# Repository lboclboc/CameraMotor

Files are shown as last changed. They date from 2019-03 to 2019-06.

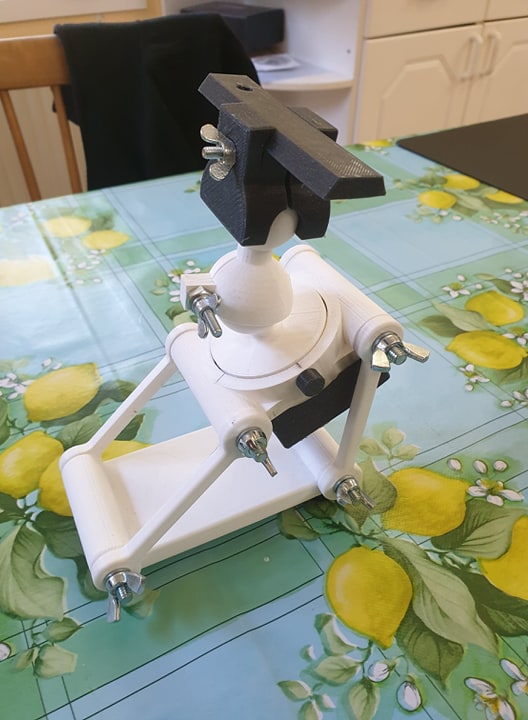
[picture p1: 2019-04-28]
Images/Finished-mount.jpg

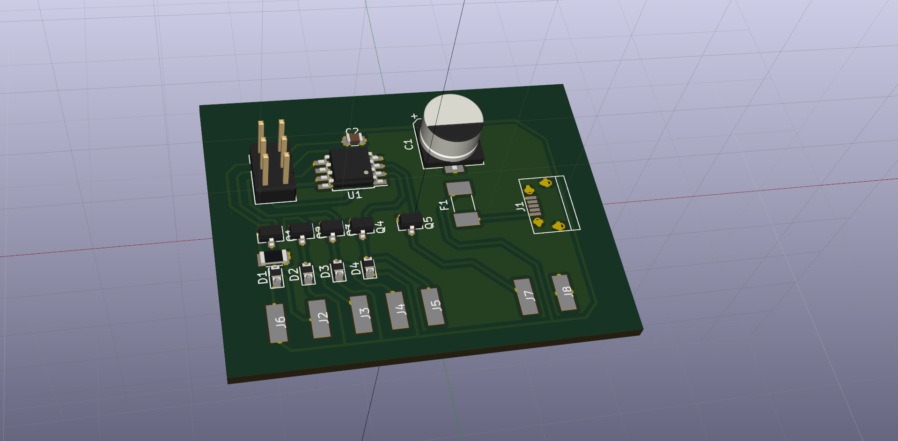
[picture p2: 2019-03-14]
CameraMotor.png

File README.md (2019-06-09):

# CameraMotor
Motorized equatorial camera mount.

This is the code for the EQ-Camera thingiverse mount at https://www.thingiverse.com/thing:3594100.
The current development is focusing on a ESP8266 wifi enabled controller that also will be able to do timelapsing for other purposes 
than astrophotographing.

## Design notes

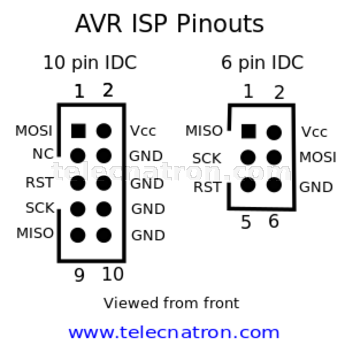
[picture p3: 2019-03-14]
avr-isp-pinout-345x.png

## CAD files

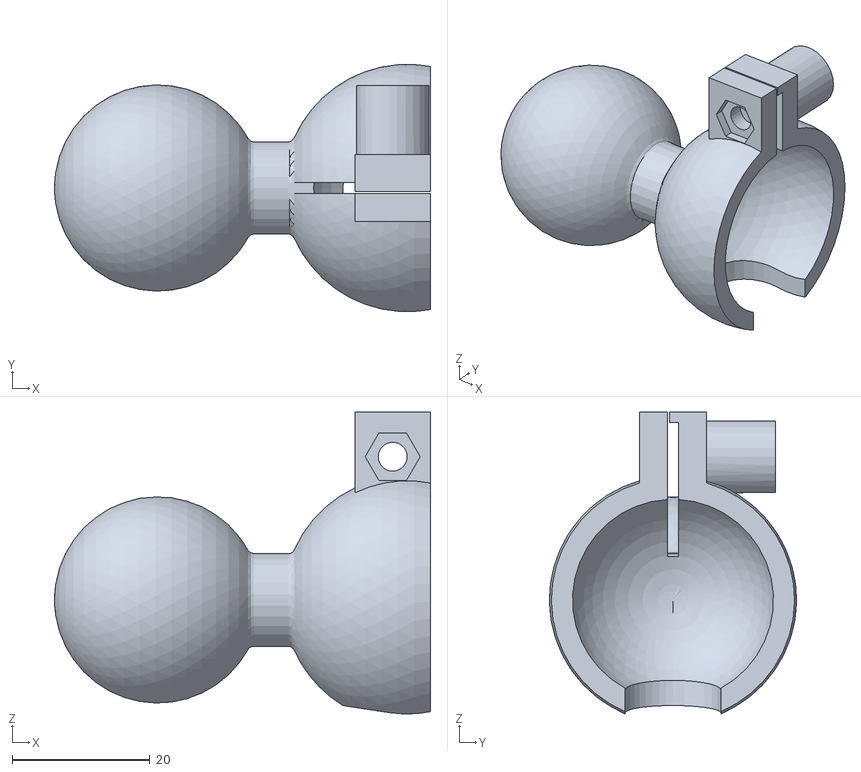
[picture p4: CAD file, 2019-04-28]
3D/CameraMount.stl
54.7 x 35.9 x 43.9

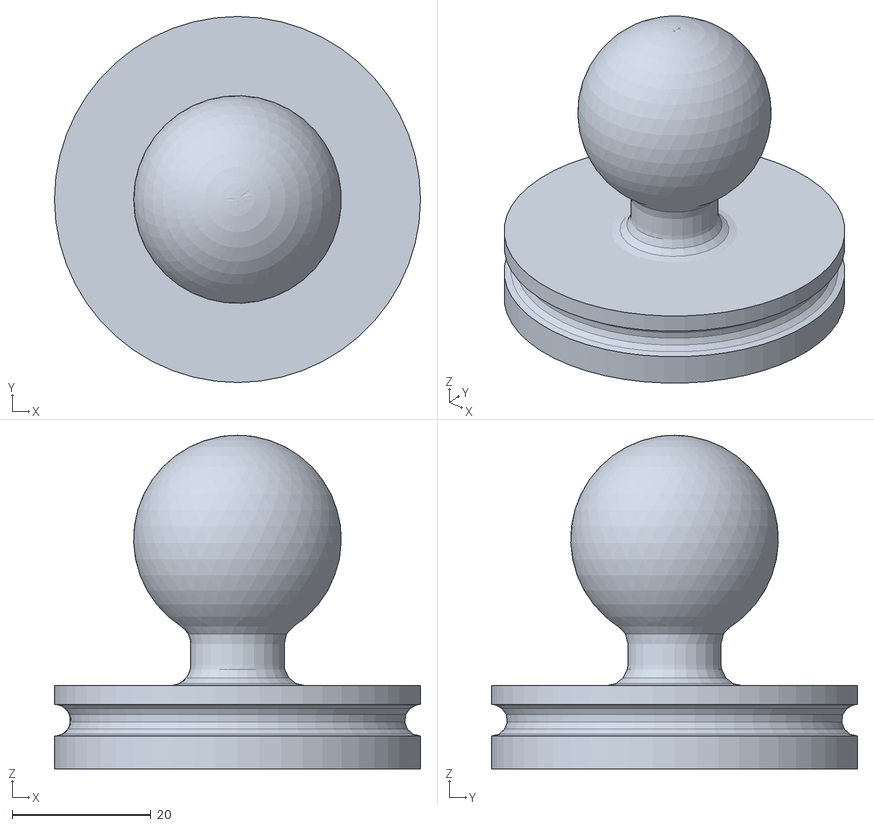
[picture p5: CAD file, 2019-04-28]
3D/turret.stl
52.8 x 52.8 x 48.1

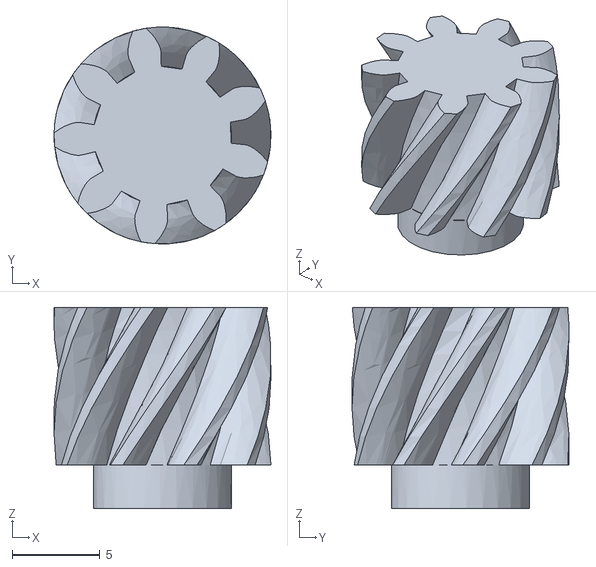
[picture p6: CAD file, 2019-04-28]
3D/Drive.stl
12.4 x 12.4 x 11.5

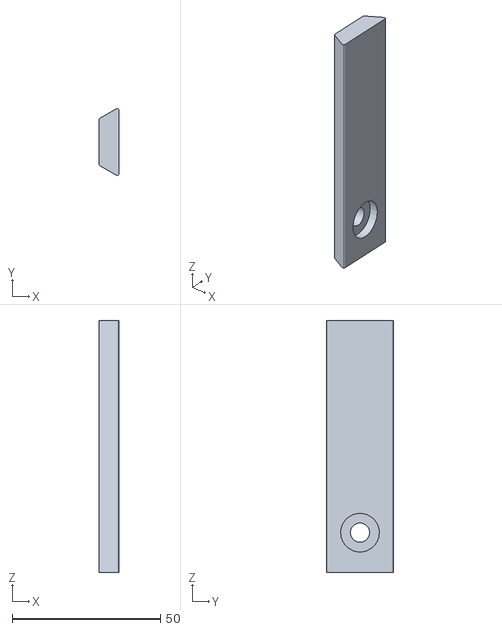
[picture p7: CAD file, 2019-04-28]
3D/CameraRail.stl
6.84 x 22.6 x 85.0

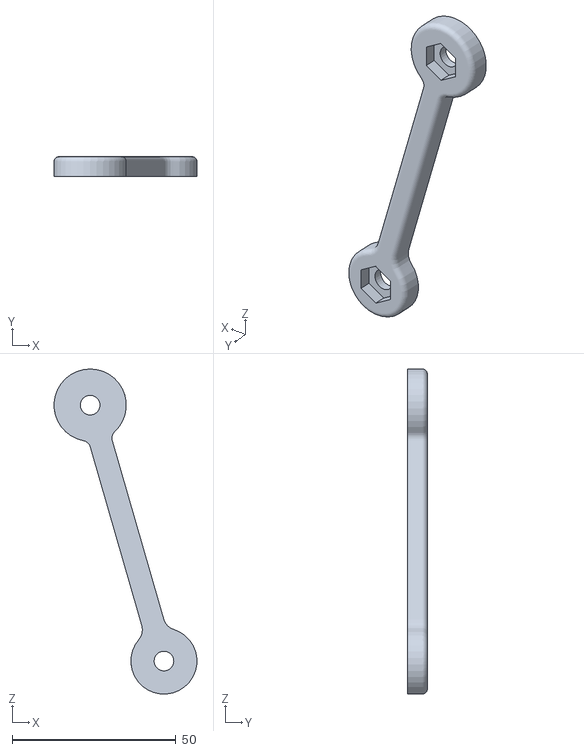
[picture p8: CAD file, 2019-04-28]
3D/arm.stl
43.5 x 6.00 x 99.1

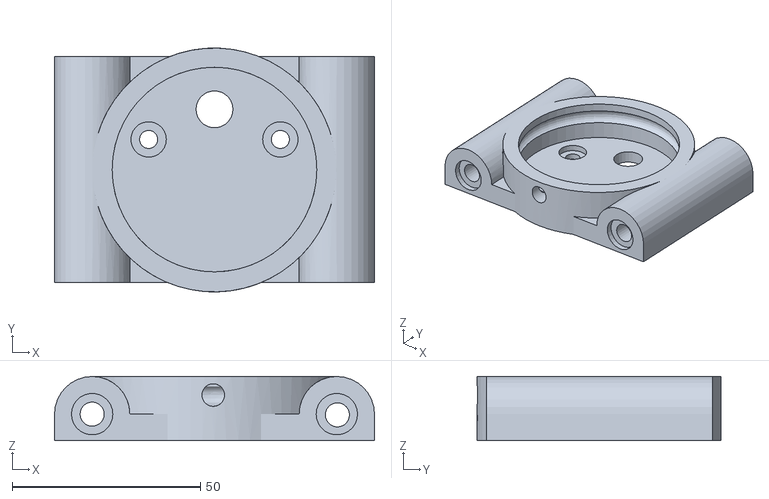
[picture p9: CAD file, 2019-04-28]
3D/topplate.stl
85.0 x 64.8 x 17.0

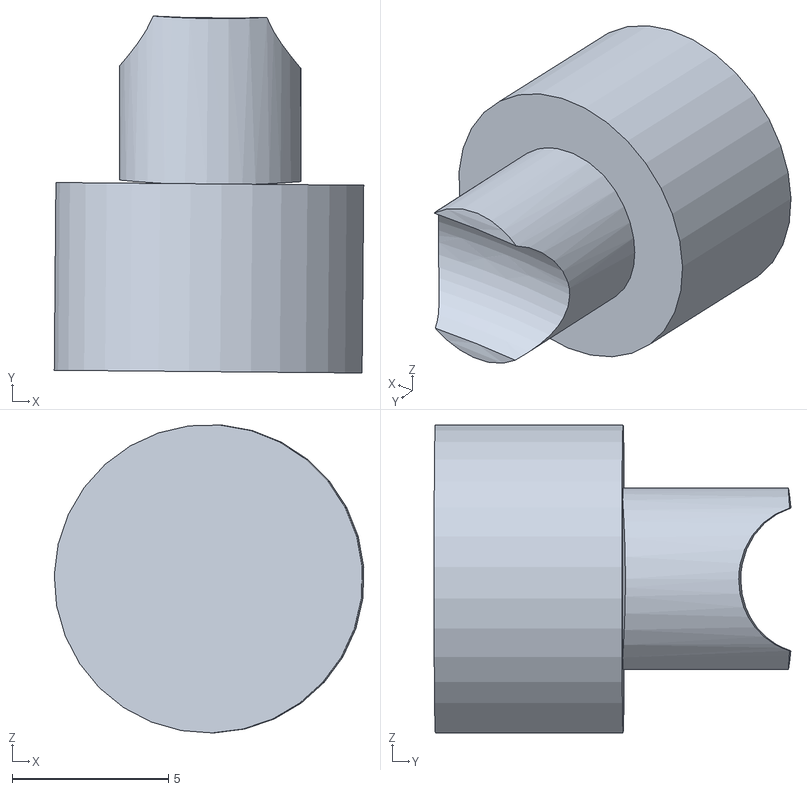
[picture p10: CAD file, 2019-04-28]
3D/Plug.stl
9.89 x 11.4 x 9.84

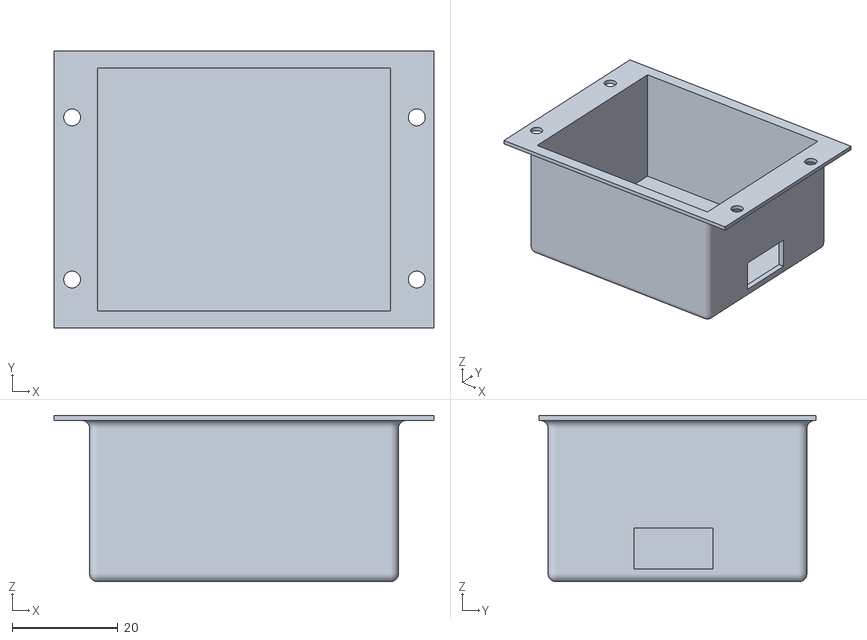
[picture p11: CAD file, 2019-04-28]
3D/PCB-Cover.stl
71.9 x 52.4 x 31.5

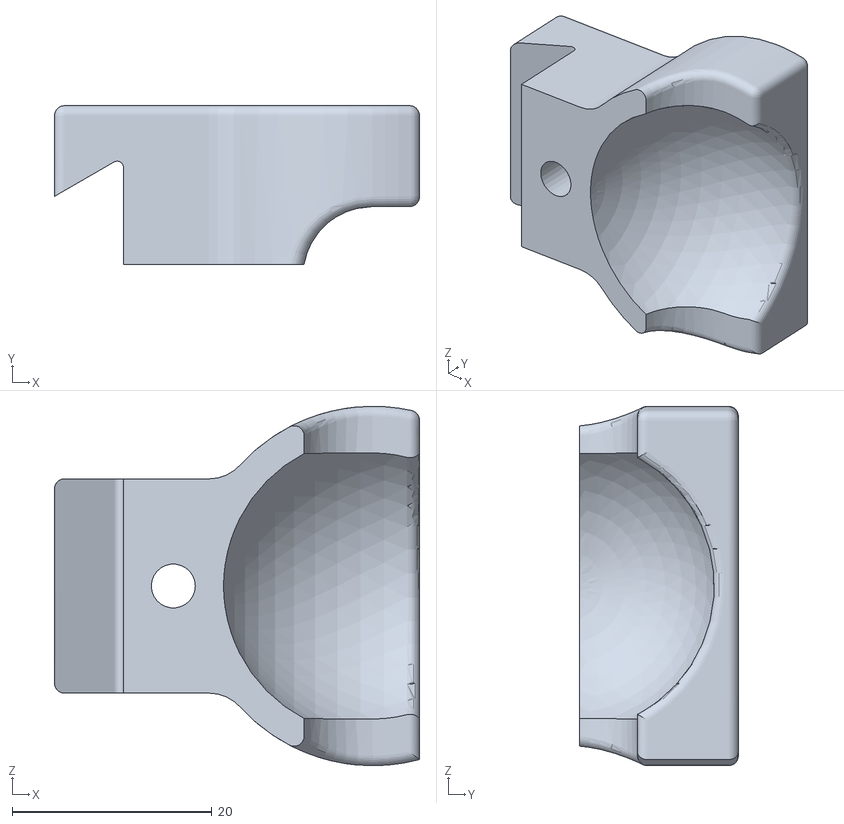
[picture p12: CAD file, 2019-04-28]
3D/CameraTilt.stl
36.6 x 15.9 x 36.0

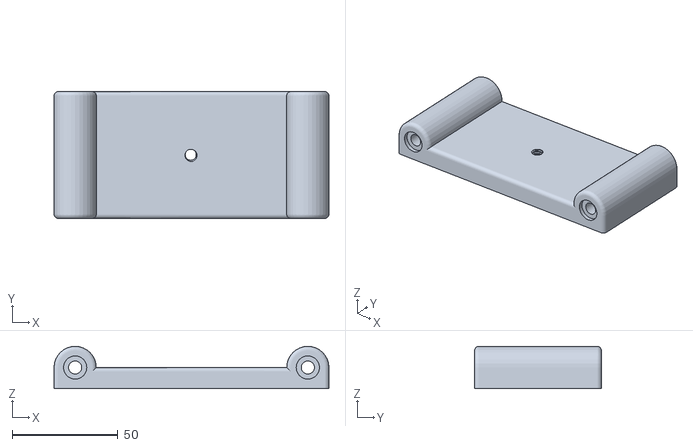
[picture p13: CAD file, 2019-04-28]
3D/bottomplate.stl
130.0 x 60.0 x 20.0

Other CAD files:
3D/CameraMotorMount.FCStd

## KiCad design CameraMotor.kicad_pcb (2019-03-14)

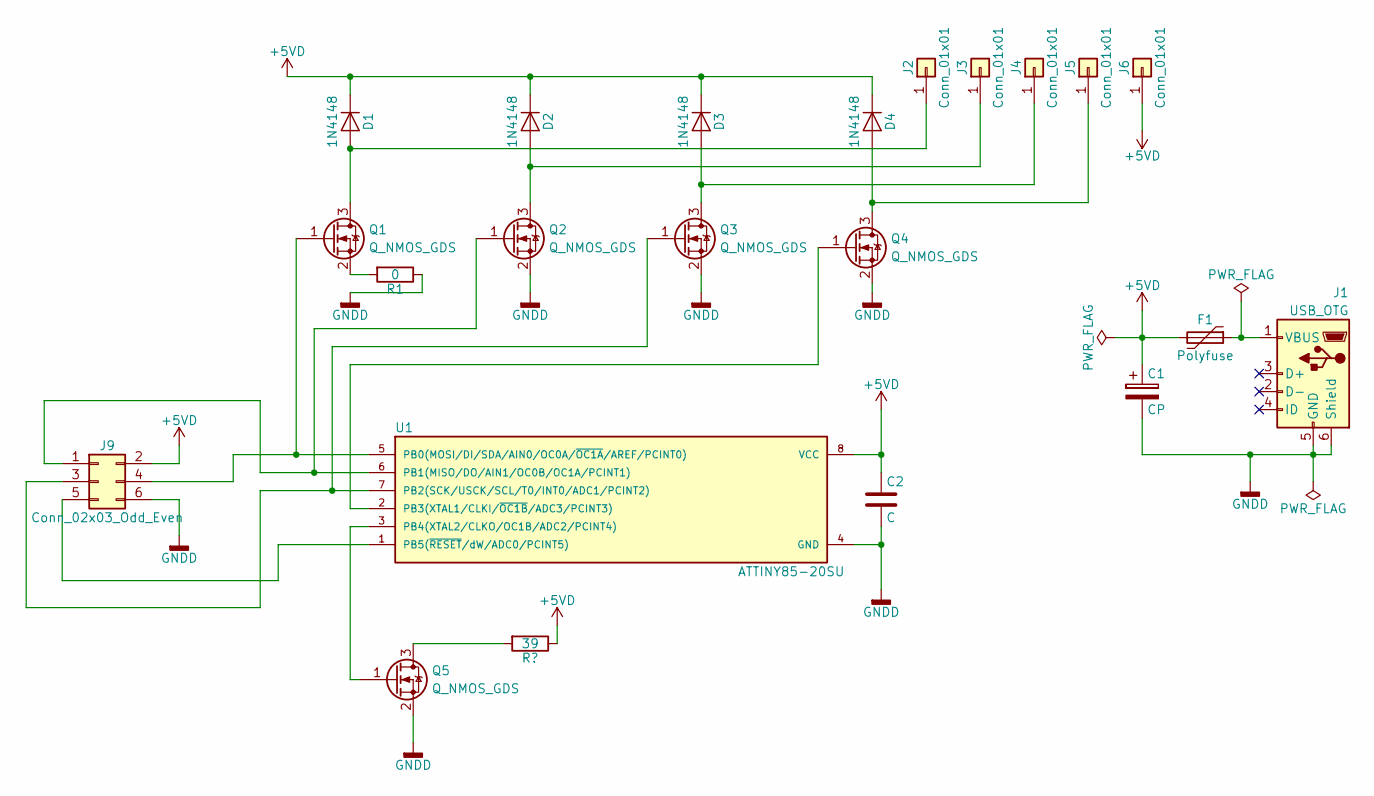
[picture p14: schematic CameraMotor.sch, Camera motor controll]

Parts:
C1: CP; CP_Elec_8x5.4
C2: C; C_0805
D1, D2, D3, D4: 1N4148; D_0805
F1: Polyfuse; Fuse_0679H
J1: USB_OTG; SOIC-28W_7.5x17.9mm_Pitch1.27mm
J2, J3, J4, J5, J6: Conn_01x01; Wire_Pad_5x2mm
J9: Conn_02x03_Odd_Even; Pin_Header_Straight_2x03_Pitch2.54mm
Q1, Q2, Q3, Q4, Q5: Q_NMOS_GDS; SOT-23
R1: 0; R_1206
U1: ATTINY85-20SU; SOIJ-8_5.3x5.3mm_Pitch1.27mm

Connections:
+5VD: C1.1, C2.1, D1.1 (K), D2.1 (K), D3.1 (K), D4.1 (K), F1.2, J6.1, J9.2, U1.8 (VCC)
GNDD: C1.2, C2.2, J1.5 (GND), J1.6 (Shield), J9.6, Q2.2 (S), Q3.2 (S), Q4.2 (S), Q5.2 (S), R1.1, U1.4 (GND); also elsewhere on the board
unnamed: D1.2 (A), J2.1, Q1.3 (D)
unnamed: D2.2 (A), J3.1, Q2.3 (D)
unnamed: D3.2 (A), J4.1, Q3.3 (D)
unnamed: D4.2 (A), J5.1, Q4.3 (D)
unnamed: F1.1, J1.1 (VBUS)
unnamed 10: Q5.3 (D); also elsewhere on the board
unnamed: J9.1, Q2.1 (G), U1.6 (PB1(MISO/DO/AIN1/OC0B/OC1A/PCINT1))
unnamed: J9.3, Q3.1 (G), U1.7 (PB2(SCK/USCK/SCL/T0/INT0/ADC1/PCINT2))
unnamed: J9.4, Q1.1 (G), U1.5 (PB0(MOSI/DI/SDA/AIN0/OC0A/~OC1A~/AREF/P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)
unnamed: J9.5, U1.1 (PB5(~RESET~/dW/ADC0/PCINT5))
unnamed: Q1.2 (S), R1.2
unnamed: Q4.1 (G), U1.2 (PB3(XTAL1/CLKI/~OC1B~/ADC3/PCINT3))
unnamed: Q5.1 (G), U1.3 (PB4(XTAL2/CLKO/OC1B/ADC2/PCINT4))

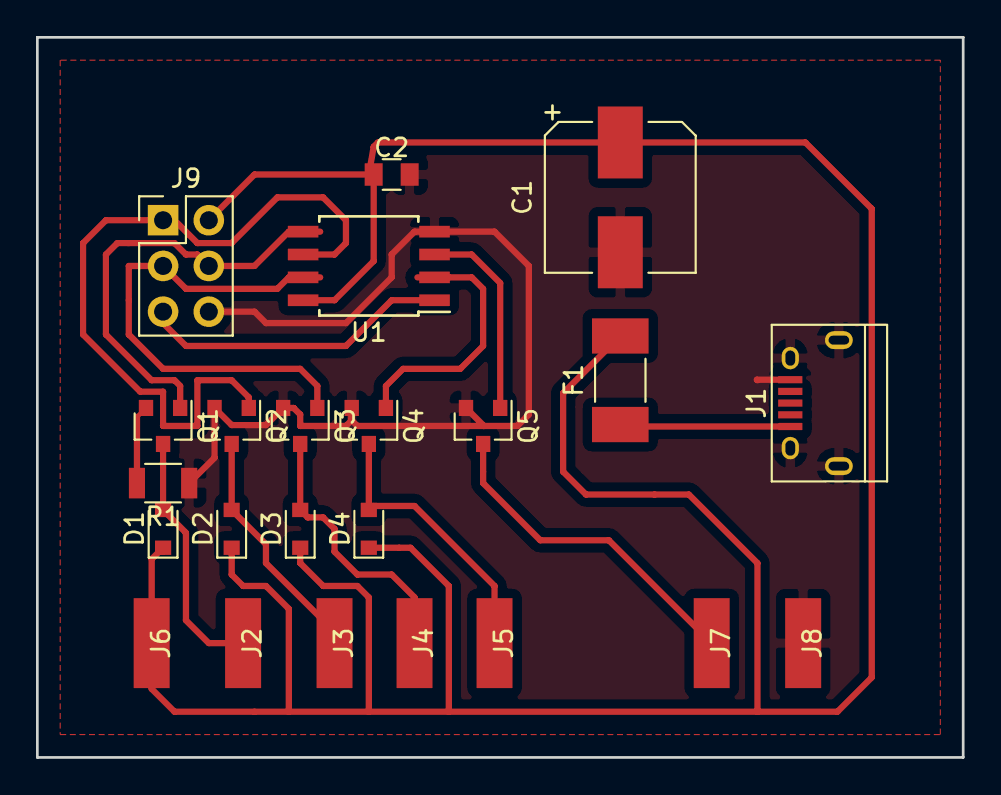
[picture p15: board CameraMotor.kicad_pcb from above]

Board: 2 copper layers, 51.4 x 40.0 mm, 23 parts (0 on the bottom side), 15 nets.

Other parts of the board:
J7, J8: Conn_01x01; Wire_Pad_5x2mm

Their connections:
GNDD: J8.1; also elsewhere on the board
unnamed 10: J7.1; also elsewhere on the board

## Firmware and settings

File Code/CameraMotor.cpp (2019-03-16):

#include <avr/io.h>
#include <avr/interrupt.h>
#include <avr/wdt.h>
#include <avr/sleep.h>


#define M1A             0
#define M2A             1
#define M1B             2
#define M2B             3
#define POWERBANK_PIN   4

#define M1      0
#define M2      1

// Timer settings.
#define COM0A_val 0 // Normal port operation, OC0A/OC0B disconnected.
#define COM0A1_val ((COM0A_val >> COM0A1) & 1)
#define COM0A0_val ((COM0A_val >> COM0A0) & 1)

#define COM0B_val 0 // Normal port operation, OC0A/OC0B disconnected.
#define COM0B1_val ((COM0B_val >> COM0B1) & 1)
#define COM0B0_val ((COM0B_val >> COM0B0) & 1)

#define WGM_val 2 // Clear Timer on Compare Match (CTC) Mode.
#define WGM02_val ((WGM_val >> WGM02) & 1)
#define WGM01_val ((WGM_val >> WGM01) & 1)
#define WGM00_val ((WGM_val >> WGM00) & 1)

#define POWERBANK_CYCLE 8500 // ms
#define POWERBANK_PULSE 750   // ms

// CLK divisor of 8 and OCRA0 11 -> 100us ticks.
#define OCRA0_COUNT 11
//#define TICKS 104462  // Ticks per step in order to make a 24h rotation.
#define TICKS 89932  // Ticks per step in order to make a 24h rotation.

//#define CS_val 5 // clk I/O /1024 (From prescaler).
//#define CS_val 3 // clk I/O /64 (From prescaler).
#define CS_val 2 // clk I/O /8 (From prescaler).
#define CS02_val ((CS_val >> CS02) & 1)
#define CS01_val ((CS_val >> CS01) & 1)
#define CS00_val ((CS_val >> CS00) & 1)

#define FOC0A_val 0 // No Compare Match
#define FOC0B_val 0 // No Compare Match

#define TOIE0_val 0 // Overflow Interrupt Enable

#define OCIE0A_val 1 // Timer/Counter0 Output Compare Match A Interrupt Enable
#define OCIE0B_val 0 // Timer/Counter0 Output Compare Match B Interrupt Enable

static unsigned char pos = 0;
static unsigned char pb_value;      // Value to use for the powerbank pin.

#define I_OFF {0,0}
#define I_FWD {1,0}
#define I_REV {0,1}

#if 1
unsigned char steps[4][2][2] = {
    {I_FWD, I_REV},
    {I_FWD, I_FWD},
    {I_REV, I_FWD},
    {I_REV, I_REV},
};
#else
unsigned char steps[8][2][2] = {
    {I_OFF, I_OFF},
    {I_FWD, I_OFF},
    {I_FWD, I_FWD},
    {I_OFF, I_FWD},
    {I_OFF, I_OFF},G
    {I_REV, I_OFF},
    {I_REV, I_REV},
    {I_OFF, I_REV},
};
#endif


unsigned char portb = 0;
unsigned short current = 0;
static void sleep(unsigned int);


void setup() {
    // All pins output.
    DDRB = 0x1F;
    
    // Timer 
    TCCR0A = (COM0A1_val << COM0A1) | (COM0A0_val << COM0A0) |
             (COM0B1_val << COM0B1) | (COM0B0_val << COM0B0) |
             (WGM01_val  << WGM01) | (WGM00_val  << WGM00);

    TCCR0B = (FOC0A_val << FOC0A) | (FOC0B_val << FOC0B) |
             (WGM02_val << WGM02) |
             (CS02_val  << CS02) | (CS01_val  << CS01) | (CS00_val  << CS00);

    TIMSK =  (OCIE0A_val << OCIE0A) | (OCIE0B_val << OCIE0B) | (TOIE0_val << TOIE0);

    OCR0A = OCRA0_COUNT;

    set_sleep_mode(SLEEP_MODE_IDLE);

    sei();
}

void update_motor() {
    unsigned char p = pos & ((sizeof steps / sizeof steps[0]) - 1);
    portb = (steps[p][M1][0] << M1A) | (steps[p][M1][1] << M1B) |
            (steps[p][M2][0] << M2A) | (steps[p][M2][1] << M2B);
    PORTB = portb;
    current = 4;
}

static void wait_char_p(unsigned char *p)
{
    cli();
    unsigned char org_value = *p;
    while(*p == org_value)
    {
        sleep_enable();
        sei();
        sleep_cpu();
        sleep_disable();
        cli();
        wdt_reset();
    }
    sei();
}

int main(int argc, char **argv)
{
    setup();
    while(1)
    {
        wait_char_p(&pos);
        update_motor();
        sleep(80);
        current = 3;
    }
}

void sleep(unsigned int ticks)
{
    while(ticks != 0) {
        sleep_enable();
        sleep_cpu();
        sleep_disable();
        ticks--;
        wdt_reset();
    }
}

void ms_tick()
{
    static unsigned int powerbank_clock = 0;
    if (++powerbank_clock > POWERBANK_CYCLE) {
        powerbank_clock = 0;
    }

    if (powerbank_clock < POWERBANK_PULSE) {
        pb_value = 1 << POWERBANK_PIN;
    }
    else {
        pb_value = 0;
    }
}

// Timer0 Interrupt 
ISR(TIMER0_COMPA_vect)
{
    static unsigned long tick = 0;
    static unsigned char pwm_step = 0;
    static unsigned int ms_prescaler = 0;

    if (++tick >= TICKS) {
        tick = 0;
        pwm_step = 0;
        pos--;
    }

    if (++ms_prescaler >= 10) {
        ms_prescaler = 0;
        ms_tick();
    }

    if (++pwm_step >= 4) {
        pwm_step = 0;
        PORTB = portb | pb_value;
    }

    if (pwm_step >= current) {
        PORTB = 0 | pb_value;
    }

}

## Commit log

2019-03-14 Initial checkin to git
    [Calculations.ods, CameraMotor.kicad_pcb, CameraMotor.sch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]
2019-03-14 Re-calibrated after full turn times.
    [Calculations.ods]
2019-03-16 Safer powerbank settings.
2019-03-17 Removed cyclic error but missing things.
    Missing PCB cover and mirrored camera mount.
    [CameraMotorMount.FCStd]
2019-03-17 Rework
    Remade the camera tilt.
    Increased the thickness
    Allow for screw to slide in the camera rail.
    [CameraMotorMount.FCStd]
2019-04-28 Imported from private SVN
    [CameraMotorMount.FCStd, CameraMount.stl, CameraRail.stl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]
